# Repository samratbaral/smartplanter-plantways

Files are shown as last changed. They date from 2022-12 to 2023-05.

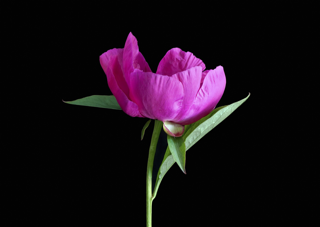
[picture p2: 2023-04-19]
src/plantways_app/Plantways-Application_client_20230317025249/assets/backgrounds/plant-purple.png

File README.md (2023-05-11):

# Smart Planter: PlantWays

Its an IOT(Internet of Things) project using Flutter development environment.
Please see the [Blog Post](https://blog.uta.edu/cseseniordesign/2023/05/10/smart-planter/) of Smart-Planter.
#
## Getting Started

Please see the [Getting Started](/src/plantsways_app/README.md) section for instructions on how to get started with this project.
#
## Summary
Please see the [Summary](/doc/summary/summary.md) of project.
#
## Design
Please see the [Design](/doc/design/3D%20print/) of project.
#
## Documentation
Please see the [Documents](/doc/documents/overleaf.md) of project.
#
## Source Code
Please see source code of the
- **[Smart Planter IoT](/src/plantsways_iot/)** and
- **[Flutter Phone Application for iOS and Android](/src/Plantways-Application_client_20230317025249/)**

For more information click [Read About the Project.](/src/README.md)
#

## Team

Our Team followed this [Contribute Guide](/CONTRIBUTE) for development information. If you have any questions, please contact by clicking the email.

**Samrat Baral:**[`samrat.baral[at] mavs [dot] uta [dot] edu`](mailto:samrat.baral@mavs.uta.edu)

**Samuel J Ruiz :**[`samuel.ruiz3[at] mavs [dot] uta [dot] edu`](mailto:samuel.ruiz3@mavs.uta.edu)

**Luis Guillermo Jaen:**[`luis.jaen[at] mavs [dot] uta [dot] edu`](mailto:luis.jaen@mavs.uta.edu)

**Don Dui:** [`don.bui[at] mavs [dot] uta [dot] edu`](mailto:don.bui@mavs.uta.edu)

**Kevin Eduardo Flores:**[`kevin.flores[at] mavs [dot] uta [dot] edu`](mailto:kevin.flores@mavs.uta.edu)

#
**NOTE: I have written this README using declarative sentences as it might appear when published. However some parts are not implemented yet.**
#

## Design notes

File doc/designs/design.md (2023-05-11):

### [< Back](/README.md) to README File.
# Design and Modeling

#### **Requirement: [LICENSE](/LICENSE), [CITATION](/CITATION.CFF)**, [AUTHORIZATION & PERMISSION](https://www.overleaf.com/login)

## **[Pot Design v1.0](/doc/design/3D%20print/Version%201/)**
This our recent Version 1.0 of 3D Design which was used to developed and tested our Smart Planter Pot. Follow the directions to view the 3D CAT Design File. or check the **[STL](/doc/design/3D%20print/Version%201/)** format.

## **[Pot Design v2.0](/doc/design/3D%20print/Version%202/)**
This our recent Version 2.0 of 3D Design which was used to developed and tested our Smart Planter Pot. Follow the directions to view the 3D CAT Design File. or check the **[STL](/doc/design/3D%20print/Version%202/)** format.

## **[Pot Design v3.0](/doc/design/3D%20print/Version%203/)**
This our recent Version 3.0 of 3D Design which was used to developed and tested our Smart Planter Pot. Follow the directions to view the 3D CAT Design File. or check the **[STL](/doc/design/3D%20print/Version%203/)** format.

#

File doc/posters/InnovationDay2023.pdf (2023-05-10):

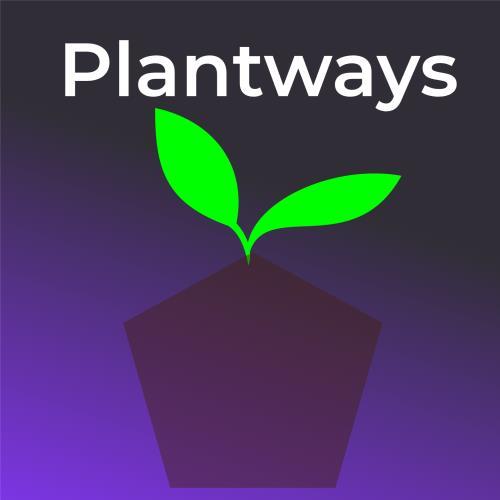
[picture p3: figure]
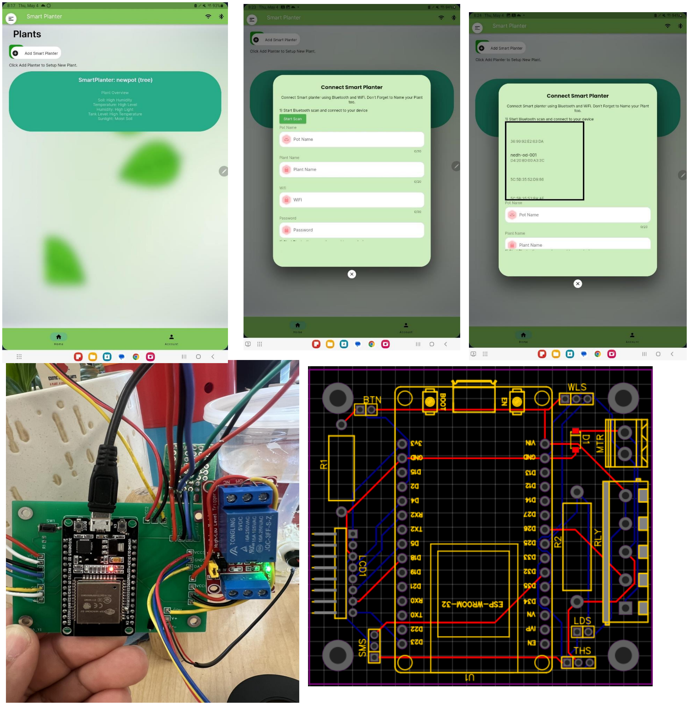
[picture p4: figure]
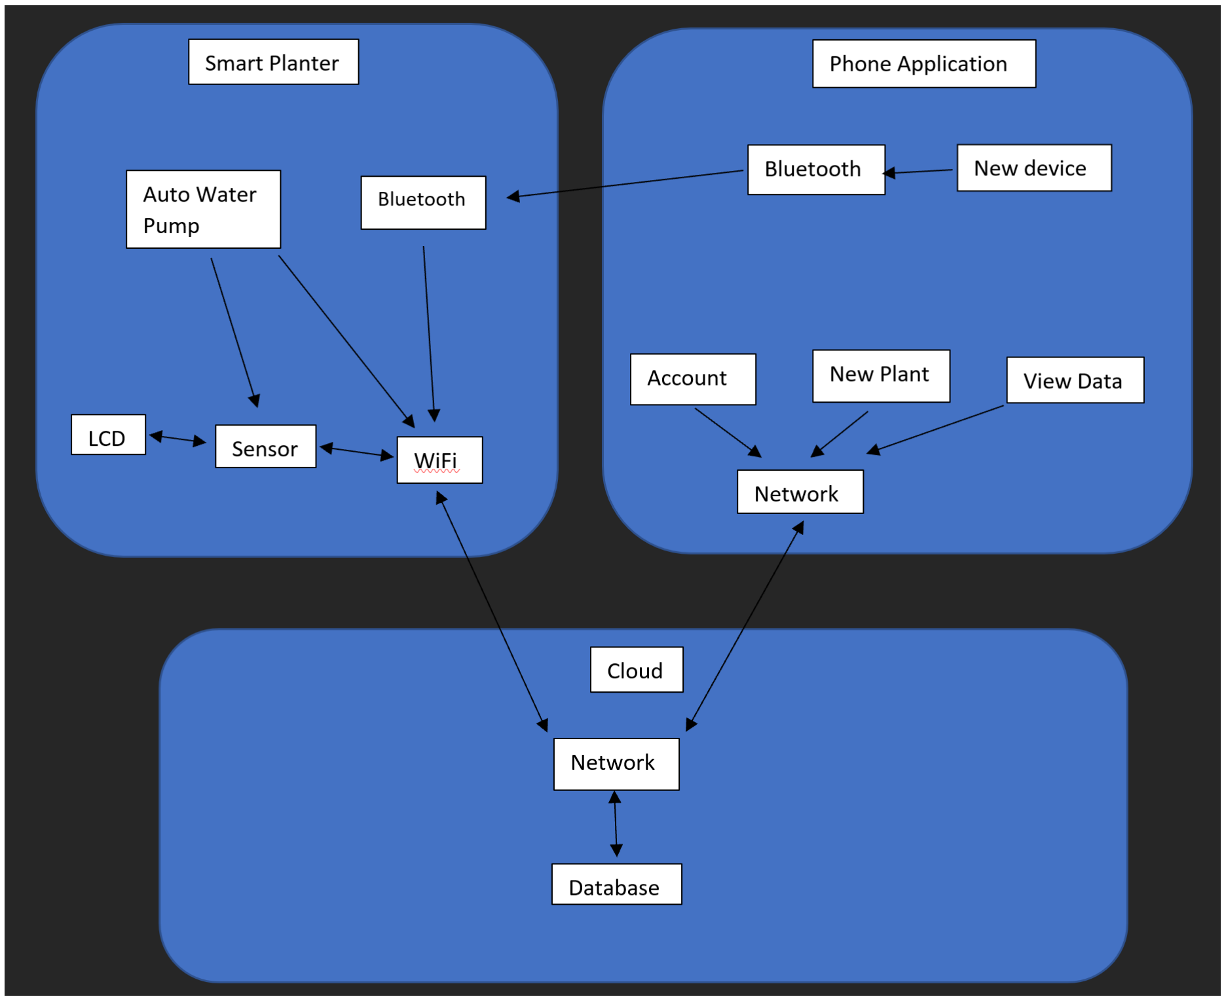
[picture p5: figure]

2023 UTA College of Engineering Innovation Day | April 18, 2023

Ruiz, S., Flores, K., Baral, S., Bui, D., Jaen, L.

# Smart Planter

Executive Summary | Key Requirements

### Background

We are going to build a self-watering plant pot, removing the consistent maintenance required in watering a house plant on your own. This pot is called the Smart Planter. The Smart Planter will measure humidity, temperature, and light exposure. We will also build an application to interface with the planter, to monitor the state for the individual plant(s). The hardware will consist of a printed circuit board and ESP32 microcontroller to minimize the size and cost of the pot.

The smart planter will solve many of the problems when it comes to doing maintenance on plants. People who have plants sitting in their house tend to forget or have a busy work schedule to take care of the plant. Therefore, the plant ends up dying, so the smart planter could be used by people who like having plants around them but do not like to take care of the plant often. The smart planter application can also be used as a learning tool for people who do not know anything about taking care of plants and want to learn how to take care of their plant by utilizing a cloud database which obtains information about the plant. For instance, some might not know how often to water a plant, so they sometimes over-water or under-water a plant, causing harmful deficiencies, which can lead to the death of the plant. Additionally, new plant caretakers could unknowingly keep their plant in an environment that’s too warm or cold for that specific species, or too dark/bright for the plant, which can also be harmful. The smart planter’s automation would remove these issues and ensure the longevity of the user's plant. The smart planter cloud database will have information about different plants, the user can pick the type of plant they are planting in the smart planter. The smart planter is designed to be used in a regular household but can also be retooled to use in a small commercial setting to grow plants on a small scale in a green house. The purpose of the smart planter is to be affordable and decorative to the public. There are some IoT planters out there, but they are expensive or have a self-watering system outside of the pot. The smart planter is supposed to combine the self-watering and IoT pot in one for ease of use.

User Interface: The Smart Planter will include a phone application that the user can use to monitor their plant. The phone application must include a user account creation section before the user is allowed to connect to their device(s). Wi-Fi/Bluetooth: The Smart Planter app must allow the users to pair to their Smart Planter device and link the device to their local network by providing their Wi-Fi name and password. Once the device is paired and set up, all the paired devices will be displayed on the home screen.
Plant Pot: The plant pot will be a 3D print design incorporating all the circuitry inside and include a refillable water tank. The design must include designated section to install the plant sensors, power cable and a reset button.
Auto Watering: The Smart Planter must be self-watering. The water pump must activate when the soil moisture indicates the plant needs water and will stop once the sensor indicates the ideal soil moisture is met.
LCD screen: The design of the plant pot will have an LCD screen in the front that must include the local time, low water tank notification, and a slideshow of sensor data.
Sensors:
- Light sensor
- Temperature sensor
- Humidity sensor
- Water level sensor

### Architectural Design Specifications

### Experimental Results

### References

### Conclusions

In the phone application subsystem, the user would be able to connect to the smart planter subsystem via Bluetooth whenever they press the new device button in their application. Once connected, they can set up their planter with their home Wi-Fi. Once their account and planter are set up both devices are connected to the network where they can send and receive data from the database. The Smart Planter sends sensor data to the LCD screen to display and to the database via Wi-Fi. The Water Pump component detects water level in the tank and sends it to sensor data. In the phone application subsystem users can view plant data, account information and plant list.

Current state of project: We currently have completed three 3D design prototypes, the initial design, the redesign, and the second larger version of the redesign. We also are done with the circuitry, and are missing some UI components, like the plant list and notification page. Currently the home page shows static values of a user's plants.

Future implementation: The finalization of the rest of the UI, like improving the user experience and stylization of the app. Completing all
the database components and making sure the correct data is sent to and from the database. Finally, completing the 3D pot most recent prototype, with complete app connectivity. We also plan on adding a list page of all the available plants to use on the pot, and a notification page which lets the user know when the water tank is low or if any of the sensor data doesn't meet the
recommended conditions for that specific plant.
- Dart Packages, https://pub.dev/.
- “The Developer Data Platform.” MongoDB, https://www.mongodb.com/.
- “Flutter Charts - Javatpoint.” Www.javatpoint.com, https://www.javatpoint.com/flutter-charts.
- Flutter Mapp, https://fluttermapp.com/.
- “Greatscott!” YouTube, YouTube, https://www.youtube.com/@greatscottlab.
- “DroneBot Workshop” YouTube, YouTube, (51) DroneBot Workshop - YouTube (https://www.youtube.com/@Dronebotworkshop)

## CSE Senior Design

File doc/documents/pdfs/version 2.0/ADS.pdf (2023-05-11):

## DEPARTMENT OF COMPUTER SCIENCE & ENGINEERING

## THE UNIVERSITY OF TEXAS AT ARLINGTON

## ARCHITECTURAL DESIGN SPECIFICATION

# CSE 4317: SENIOR DESIGN II SPRING 2023

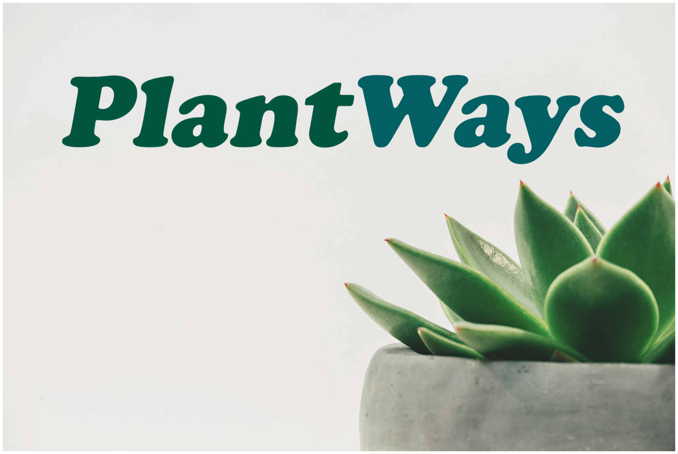
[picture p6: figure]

## PLANT WAYS

## SMARTPLANTER

SAMUEL J RUIZ
KEVIN FLORES
LUIS GUILLERMO JAEN
DON BUI
SAMRAT BARAL
Plant Ways - Spring 2023 | page 1 of 22

REVISION HISTORY

Revision | Date | Author(s) | Description
0.1 | 10.28.2022 | KF,DB,SR,LJ,SB | document creation
1.0 | 11.07.2022 | KF,DB,SR,LJ,SB | complete draft
2.0 | 12.14.2022 | KF,DB,SR,LJ,SB | final version

CONTENTS

1 Introduction | 5
2 System Overview | 6
3 Subsystem Definitions & Data Flow | 8
4 Smart Planter Subsystems | 9
5 User Interface Layer Subsystem | 15
6 Cloud Layer Subsystems | 21

LIST OF FIGURES

1 | SmartPlanter architectural layer diagram | | 6
2 | Sub-system overview | | 8
3 | Subsystem description diagram | | 9
4 | Subsystem description diagram | | 10
5 | Subsystem description diagram | | 11
6 | Subsystem description diagram | | 12
7 | Subsystem description diagram | | 13
8 | Setup subsystem description diagram | | 15
9 | Setup subsystem | | 16
10 | Account subsystem | | 18
11 | Network subsystem | | 19
12 | Cloud subsystem description diagram | | 21
13 | Cloud subsystem description diagram | | 22

LIST OF TABLES

2 | Water pump interfaces | | 10
3 | Sensors interfaces | | 11
4 | WiFi interfaces | | 12
5 | Bluetooth interfaces | | 13
6 | LCD Screen interfaces | | 14
7 | Setup Subsystem Interfaces | | 17
8 | Account Subsystem Interfaces | | 18
9 | Network Subsystem Interfaces | | 20
10 | Cloud Network Interfaces | | 21
11 | Cloud Database interfaces | | 22

### 1 INTRODUCTION

The SmartPlanter is a product intended to ease plant maintenance by monitoring the plants environment and automating the watering process. The SmartPlanter will require a mobile application that allows users to pair their SmartPlanter device to the internet. Using the mobile application, the users can set the sensor calibration data for the specific plant they are planting. The SmartPlanter device will be able to monitor the plant’s environment using the sensors and the calibration data in order to automate the watering process when the soil is too dry.

### 2 SYSTEM OVERVIEW

The SmartPlanter has three layers which consist of the SmartPlanter Layer, the User Interface layer or Phone Application Layer, and the Cloud Layer. The SmartPlanter layer consist of the physical plant pot and includes the micro-controller, water tank, sensors and LCD screen. The SmartPlanter layer monitors the plant’s environment and provides automatic watering. This layer also provides data to the Cloud Layer for storage. The User interface layer consist of a mobile phone application where the settings for the pot can be selected. This settings can be applied directly to the SmartPlanter Layer by communicating by Bluetooth. The User Interface layer can also access the SmartPlanter through the cloud layer using WiFi.

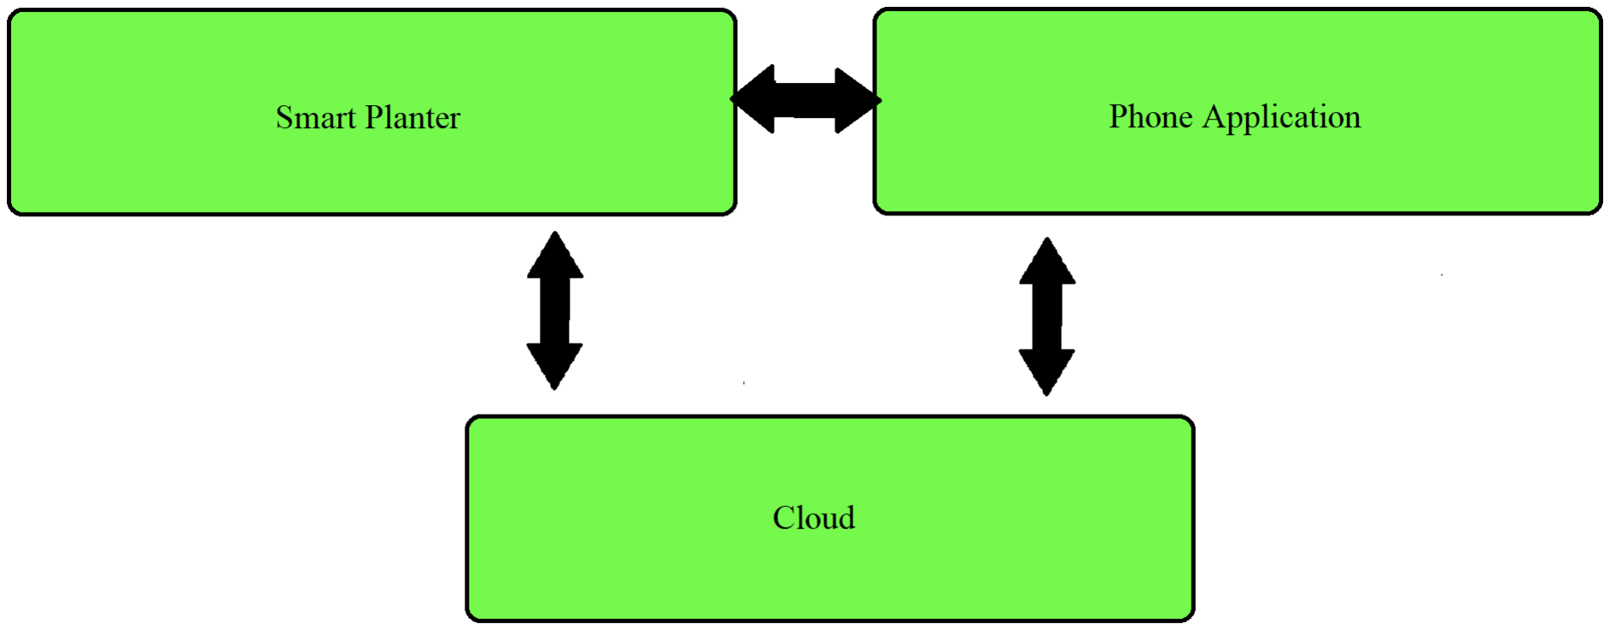
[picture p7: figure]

Figure 1: SmartPlanter architectural layer diagram

### 2.1 SMARTPLANTER

The SmartPlanter will have a display on the pot, that will let the user switch the display to show the current time. The SmartPlanter pot will have WiFi and Bluetooth. The WiFi is used to connect to the database and to upload data collected from the sensors. The Bluetooth feature will be used for the initial setup to connect it to the WiFi. The SmartPlanter pot will have a water pump used to water the plant when the soil moisture is detected low. The SmartPlanter will also include a light detector, a humidity and temperature sensor to monitor the average environment the plant is currently in and will upload the average data to the database. A water level detector will also be used to monitor the water tank level and assure it does not run below the minimum threshold. An LCD screen will also be included in the front of the SmartPlanter pot that displays either the name of the plant or the current time.

### 2.2 USER INTERFACE

The User Interface layer consist of mobile phone application that interfaces with the SmartPlanter via Bluetooth and the cloud via WiFi . The main usage of Bluetooth consist of the initial device set up to connect the SmartPlanter to the home network. The application will consist of an account subsystem to allow the user to change settings. The phone application can also change the calibration data of the SmartPlanter by adding custom settings catered to the plant they are growing. This is performed by allowing the user to connect to the cloud layer and view a database of plants. When this information is selected, it will store those calibration settings in the database and into the local storage of the Smart-

Planter. The application can also view the current environmental conditions of the plant by connecting to the cloud through the network and then accessing the SmartPlanter.

### 2.3 CLOUD

The Cloud Layer consist of a database used to store plant sensor data from the SmartPlanter and user account settings from the User Interface Layer. The database will also store hard-coded plant information that the user will be able to retrieve via the mobile phone application.

### 3 SUBSYSTEM DEFINITIONS & DATA FLOW

The user would be able to connect to the smart planter through Bluetooth whenever they press the new device button in their application once connected they can set up their planter with their home WiFi. Once their account and planter are set up both devices are connected to the network where they can send and receive data from the database.

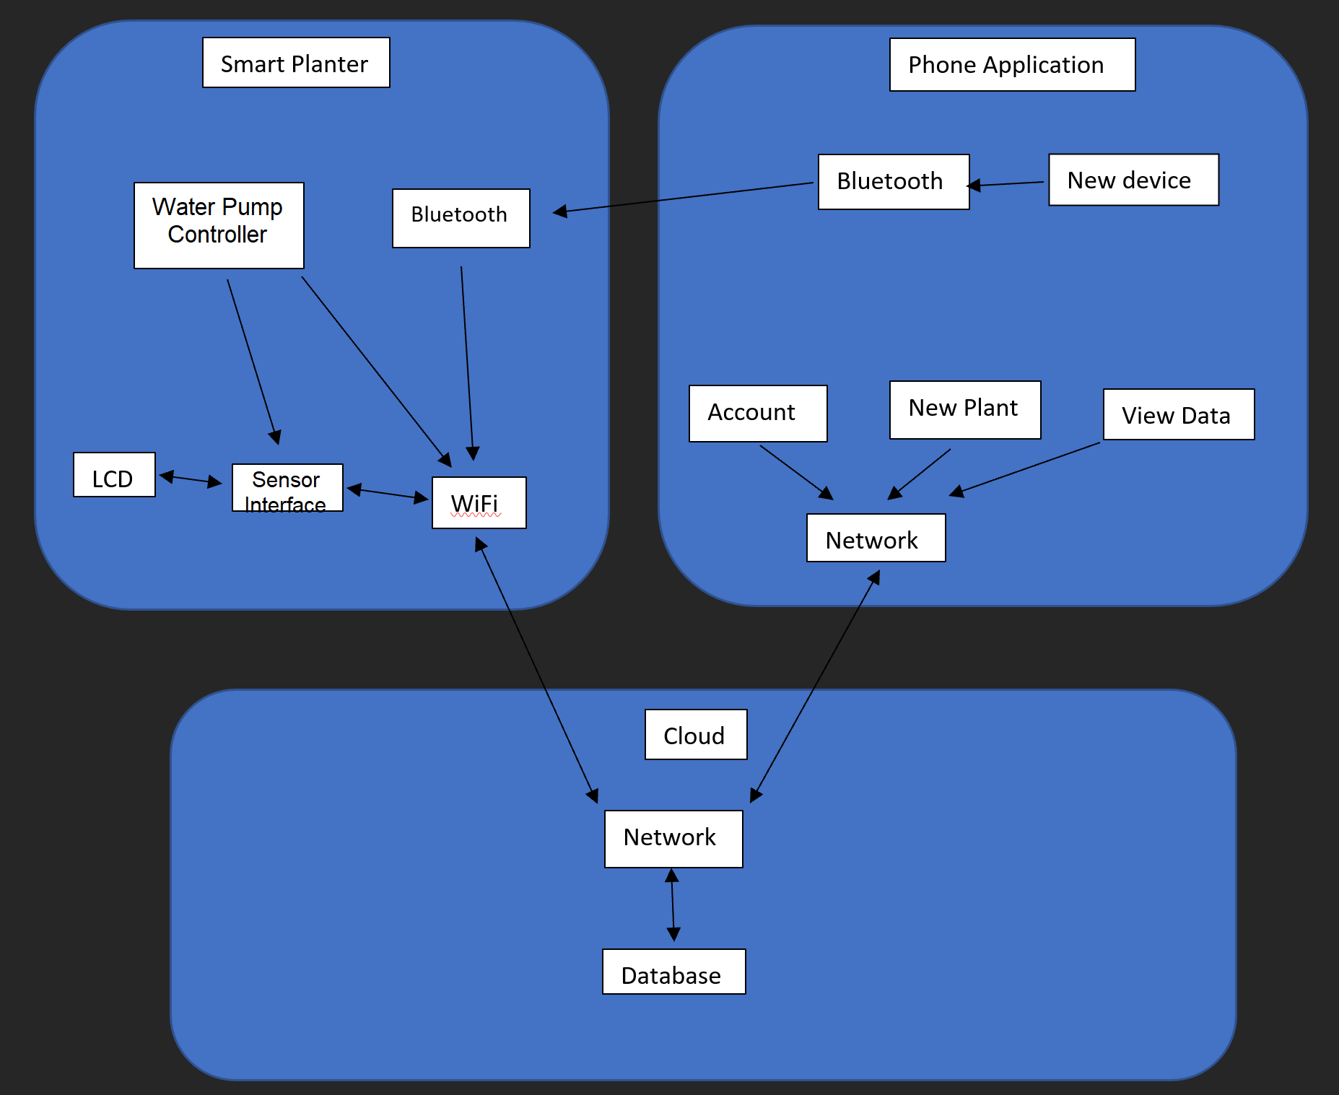
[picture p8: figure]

Figure 2: Sub-system overview

### 4 SMART PLANTER SUBSYSTEMS

The Smart Planter layer is made up of 5 different subsystems which gather information, communicate with other important functions like watering and online data, and display information to the user. The subsystems are the following: auto water pump system, sensor system, Bluetooth, WiFi, and the LCD screen.

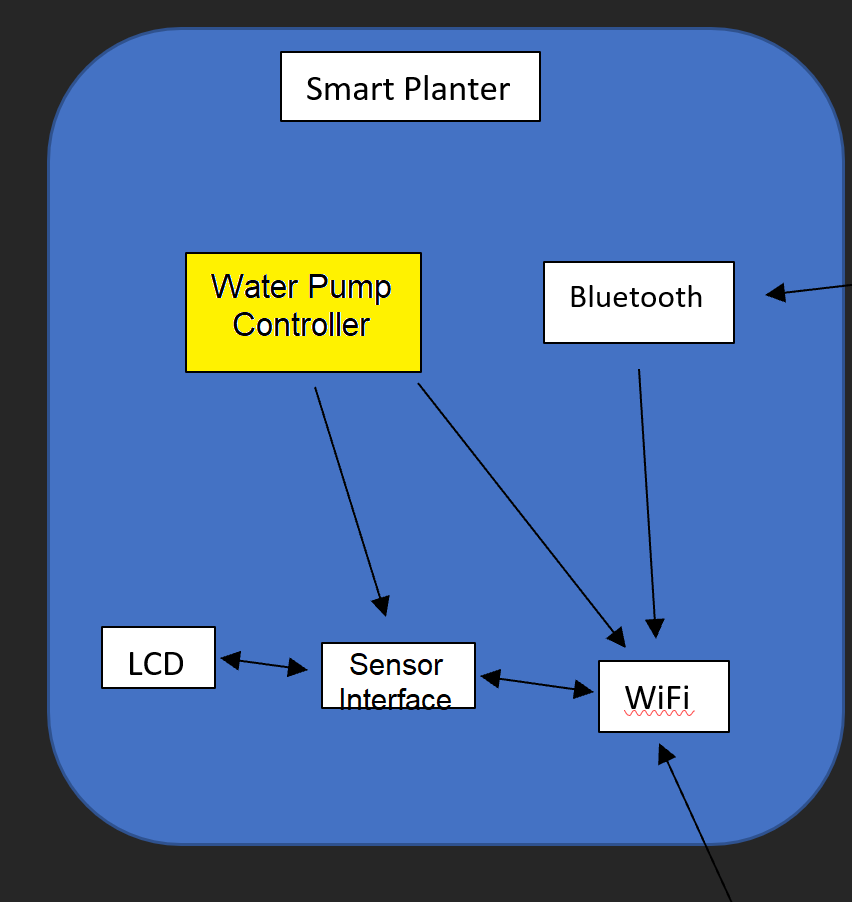
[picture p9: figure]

Figure 3: Subsystem description diagram

### 4.1 AUTO WATER PUMP

The auto water pump subsystem is in charge of watering the plant and keeping the plant at a sufficient level of moisture. It communicates with the sensors in the planter, receiving the instruction to pump water.

### 4.1.1 ASSUMPTIONS

We assume the water pump successfully receives the signal to water the planter from the moisture sensor.

### 4.1.2 RESPONSIBILITIES

This water pump subsystem is responsible for keeping the plant at a sufficient level of moisture. When the soil runs too dry, the water pump will receive a signal from the moisture sensor, which will initiate the process of pumping the water into the soil.

### 4.1.3 WATER PUMP INTERFACES

Table 2: Water pump interfaces

ID | Description | Inputs | Outputs
#01 | Moisture Sensor | moisture level | water instruction

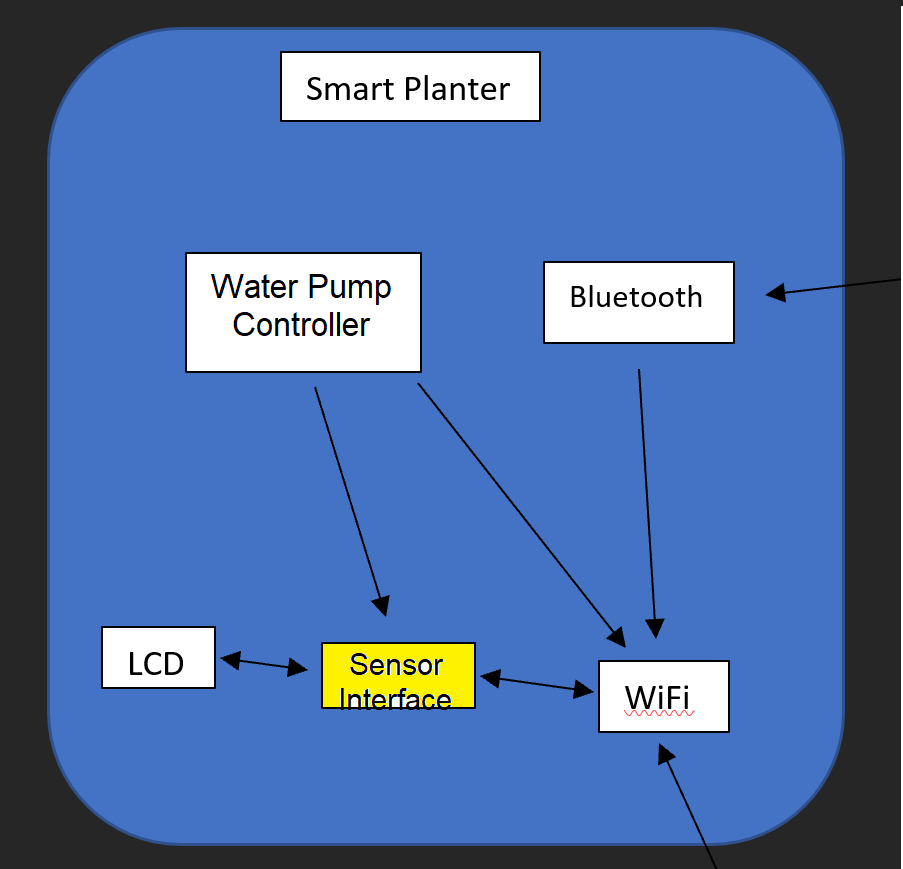
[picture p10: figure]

Figure 4: Subsystem description diagram

### 4.2 SENSORS

The sensors in our smart planter collect external and internal data which is used to monitor the current status of the plant. The sensors include: light, humidity, temperature, and soil moisture. The soil moisture sensor communicates with the water pump, telling it when to pump water, and the other 3 sensors send their data through WiFi to our cloud.

### 4.2.1 ASSUMPTIONS

We assume all of the sensors operate accurately, and correctly record data on the external and internal environments.

### 4.2.2 RESPONSIBILITIES

The light sensors are responsible for gathering data from the smart planter’s light environment, recording the light exposure on the plant. The humidity and temperature sensors are responsible for recording the humidity and temperature of the environment. The soil moisture sensor is in charge of keeping track of the moisture levels of the soil, notifying the water pump to water when the soil is too dry. All of these sensors communicate with our cloud database through WiFi.

### 4.2.3 SENSORS INTERFACES

Table 3: Sensors interfaces

ID | Description | Inputs | Outputs
#01 | Water Pump | power on for pump | water the planter

#01 | WiFi | Humidity, Temper-ature, Light Expo-sure Data | send data to cloud

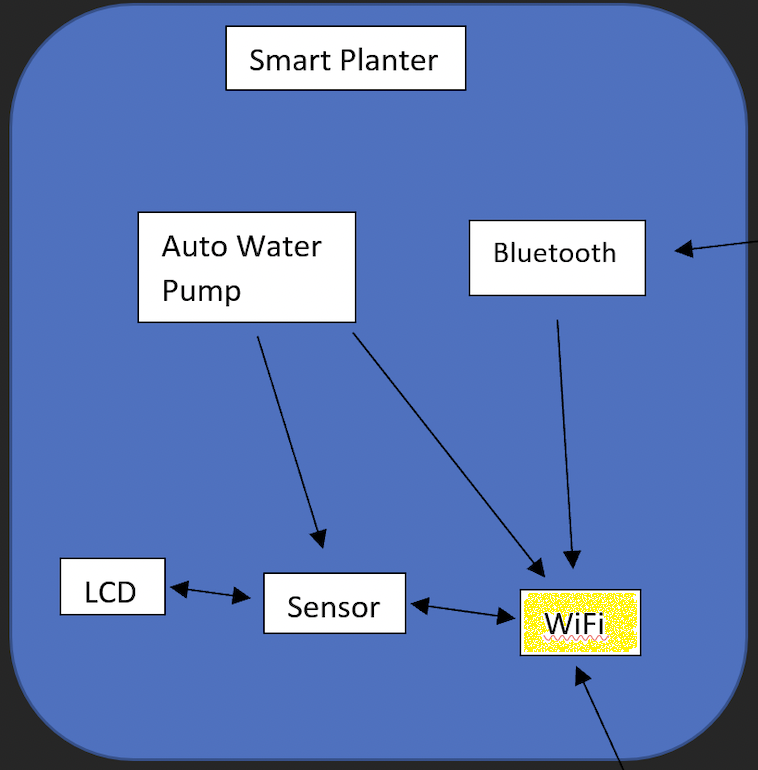
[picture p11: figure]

Figure 5: Subsystem description diagram

### 4.3 WIFI

The WiFi component of our smart planter deals with receiving all of the data from the external and internal sensors, and then sending that data off to the cloud database. The WiFi communicates with the sensor subsystem and the LCD screen.

### 4.3.1 ASSUMPTIONS

We assume the networks are up and fully operational, and that there are no obstructions to the transmission of data.

### 4.3.2 RESPONSIBILITIES

The WiFi system is responsible for receiving the light exposure, temperature, and humidity levels, and sending them over to the cloud database. It is also responsible for receiving the current time from the network and sending it over to the LCD screen.

### 4.3.3 WIFI INTERFACES

Table 4: WiFi interfaces

ID | Description | Inputs | Outputs
#01 | Light Sensor | exposed light | lumen value

#02 | Humidity Sensor | environment hu-midity | humidity percent-age

#03 | Temperature Sensor | environment tem-perature | degrees Fahren-heit

#04 | LCD Screen | current time or plant name | current time or plant name on the screen

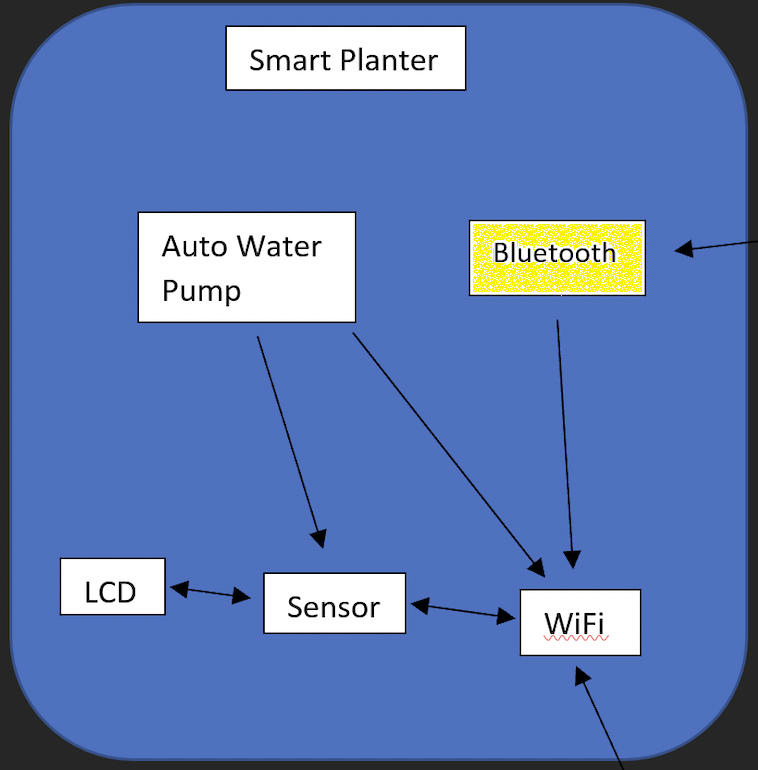
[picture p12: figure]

Figure 6: Subsystem description diagram

### 4.4 BLUETOOTH

The Bluetooth system is there to establish a connection between the smart planter and the network, via your smart phone. The Bluetooth communicates with the WiFi subsystem.

### 4.4.1 ASSUMPTIONS

We assume the Bluetooth technology is properly establishing connections between the smart planter and network.

### 4.4.2 RESPONSIBILITIES

The Bluetooth is responsible for establishing the network connection between the smart planter and WiFi, by using your smart phone to input the required information.

### 4.4.3 BLUETOOTH INTERFACES

Table 5: Bluetooth interfaces

ID | Description | Inputs | Outputs
#01 | Smart Phone | Bluetooth creden-tials | WiFi credentials

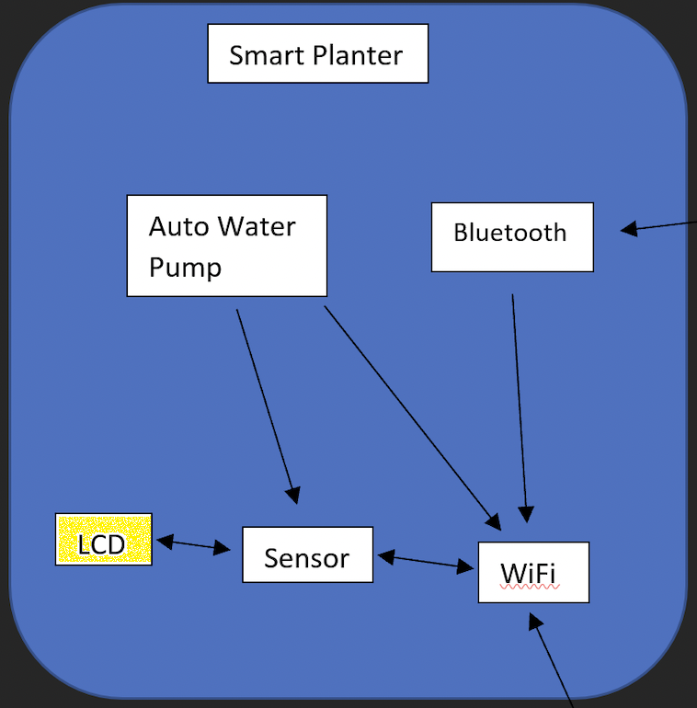
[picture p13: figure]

Figure 7: Subsystem description diagram

### 4.5 LCD SCREEN

The LCD screen is used to display either the current time or the name of your plant. The LCD screen communicates with the WiFi subsystem, receiving necessary data.

### 4.5.1 ASSUMPTIONS

We assume the LCD screen is posting the accurate plant name choice from the user, or the current time.

### 4.5.2 RESPONSIBILITIES

The LCD screen is responsible for displaying the current accurate time or name of the plant. It’s responsible for communicating with the WiFi, in order to receive the data it needs to display.

### 4.5.3 LCD SCREEN INTERFACES

Table 6: LCD Screen interfaces

ID | Description | Inputs | Outputs
#01 | WiFi | name created by the user or time chosen | Plant Name or Current Time

### 5 USER INTERFACE LAYER SUBSYSTEM

In this section, the user interface is layout where user can observe and optimize the smart planter pot. This is an application layer from the main system where users are required to create an account, where user must acknowledge and accept term and conditions to use the application in their mobile devices and its features. The application will be a GUI mobile app or mobile website GUI application the user can visit to have a unique experience.

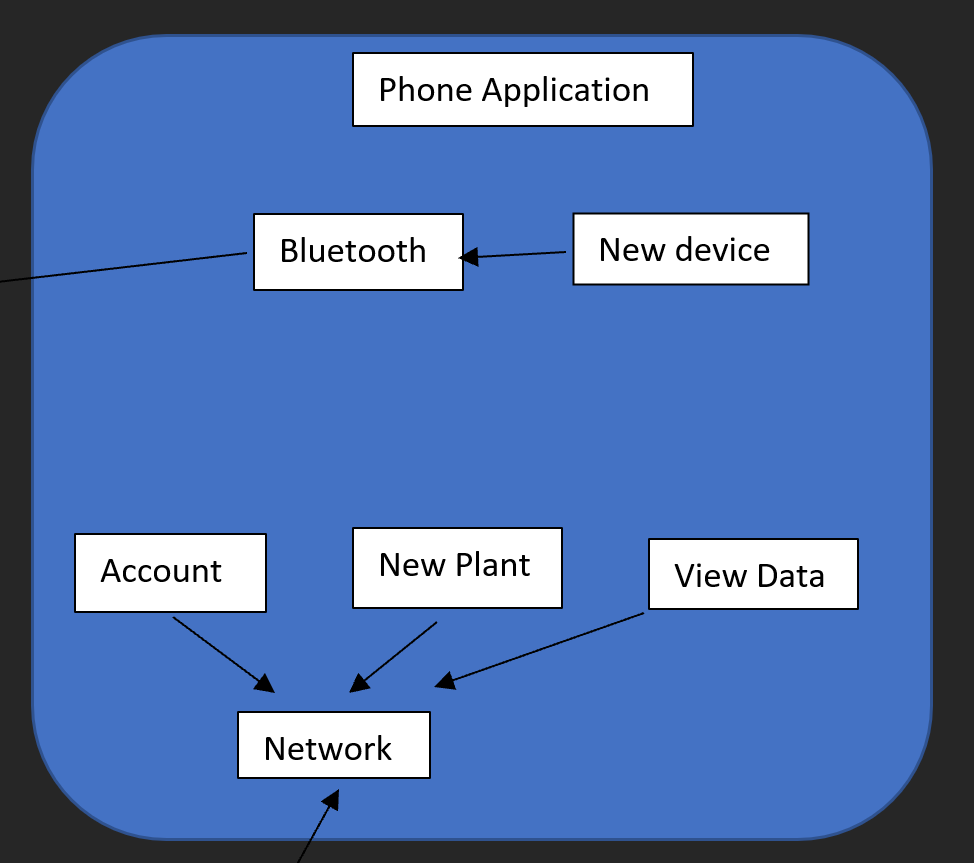
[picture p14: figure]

Figure 8: Setup subsystem description diagram

### 5.1 SETUP LAYER SUBSYSTEM

This subsystem is a setup process for a user to use smart planter pot. The user is required to agree the smart planter terms and condition so that user can register and setup their account with smart planter. The user is given registration form where user is required to input some information while other information could be optional which gives user personalized system setting while using the application.

### 5.1.1 ASSUMPTIONS

The user is assumed to have a device which is WiFi and Bluetooth enable which should be running recent Android (Version 13.0) or iOS (Version 16.0) operating system can should be capable to connect to the internet. We also assume that user read all terms and conditions before registering and using the smart planter service.

### 5.1.2 RESPONSIBILITIES

This sub-layer is responsible creating a account for a user so they can use the smart planter pot. The account creation is important for the process to have control over. After the account is created it will interact with the pot "Smart Planter Layer" and database from the "Cloud Layer" for privacy, usage and safety of the user and the application.

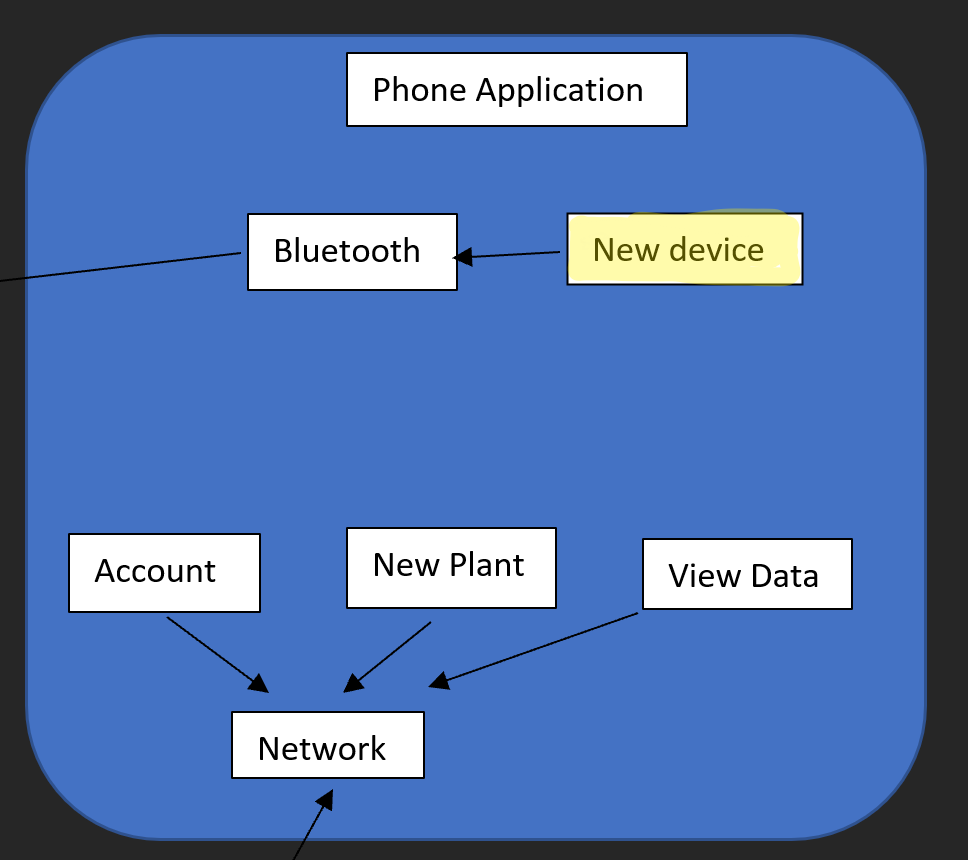
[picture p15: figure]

Figure 9: Setup subsystem

### 5.1.3 SUBSYSTEM INTERFACES

Since, This sub-layer is responsible creating a account for a user. The following are important inputs and outputs for the subsystem in the table entry for each labeled interface that connects to this subsystem. For each entry, describe any incoming and outgoing data elements will pass through this interface.

Table 7: Setup Subsystem Interfaces

ID | Description | Inputs | Outputs
#01 | User Setup (Register Form) | User Id Username First Name Last Name Email Phone Number Password Confirm Password | User Data Created

#02 | Device Setup (Register Form) | Device Id Device Name Device Picture Device Information Device Data | Device Data Created

#03 | Cloud Setup (Automatic) | User Setup Data Device Setup Data | Cloud Data Created

### 5.2 ACCOUNT SUBSYSTEM LAYER

This subsystem is a user account after setup for a registered user to use smart planter pot. The user is required to log-in so that user can use their account with their own smart planter. The user is given login form where user is required to input user credential which gives user personalized system setting while using the application.

### 5.2.1 ASSUMPTIONS

The user is assumed to have the Smart Planter mobile application is downloaded from recent Android (Version 13.0) or iOS (Version 16.0) operating system which should be capable to connect to the internet from the device using WiFi and Bluetooth enable.

### 5.2.2 RESPONSIBILITIES

This sub-layer is responsible for logging a user so they can use smart planter pot. After the user is logged in it will interact with the pot "Smart Planter Layer" and database from the "Cloud Layer" for privacy, usage and safety of the user and the application.

### 5.2.3 SUBSYSTEM INTERFACES

Since, This sub-layer is responsible logging a current account of a user. The following are important inputs and outputs for the subsystem in the table entry for each labelled interface that connects to this subsystem. For each entry, describe any incoming and outgoing data elements will pass through this interface.

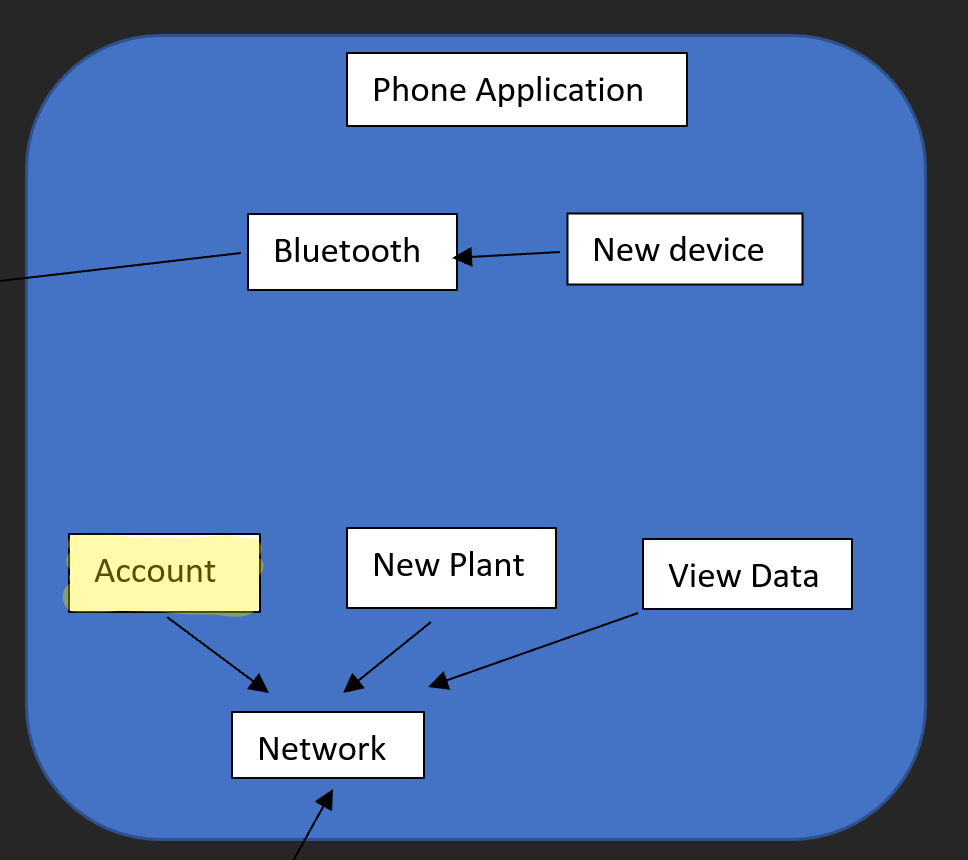
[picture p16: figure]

Figure 10: Account subsystem

Table 8: Account Subsystem Interfaces

ID | Description | Inputs | Outputs
#01 | User Validation (Login Form) | Username or Email Password | User Authentication

#03 | Pot Data (Automatic) | N/A | User Device Data

### 5.3 NETWORK SUBSYSTEM LAYER

This subsystem is a connection process for a user to use smart planter pot. The user will automatically fetch data from the database as well as it can calibrate and configure the device using internet via WiFi. The user is given registration form where user is required to input some information while other information could be optional which gives user personalized system setting while using the application.

### 5.3.1 ASSUMPTIONS

The user are assumed to have a device which is WiFi and Bluetooth enable which should be running recent Android (Version 13.0) or iOS (Version 16.0) operating system with the Smart Planter mobile application which is logged-in user which is capable of connecting to the internet.

### 5.3.2 RESPONSIBILITIES

This sub-layer is responsible connecting a account for a user so they can use the smart planter pot online. After the account is connected it will interact with the pot "Smart Planter Layer" and database from the "Cloud Layer" for any data exchange.

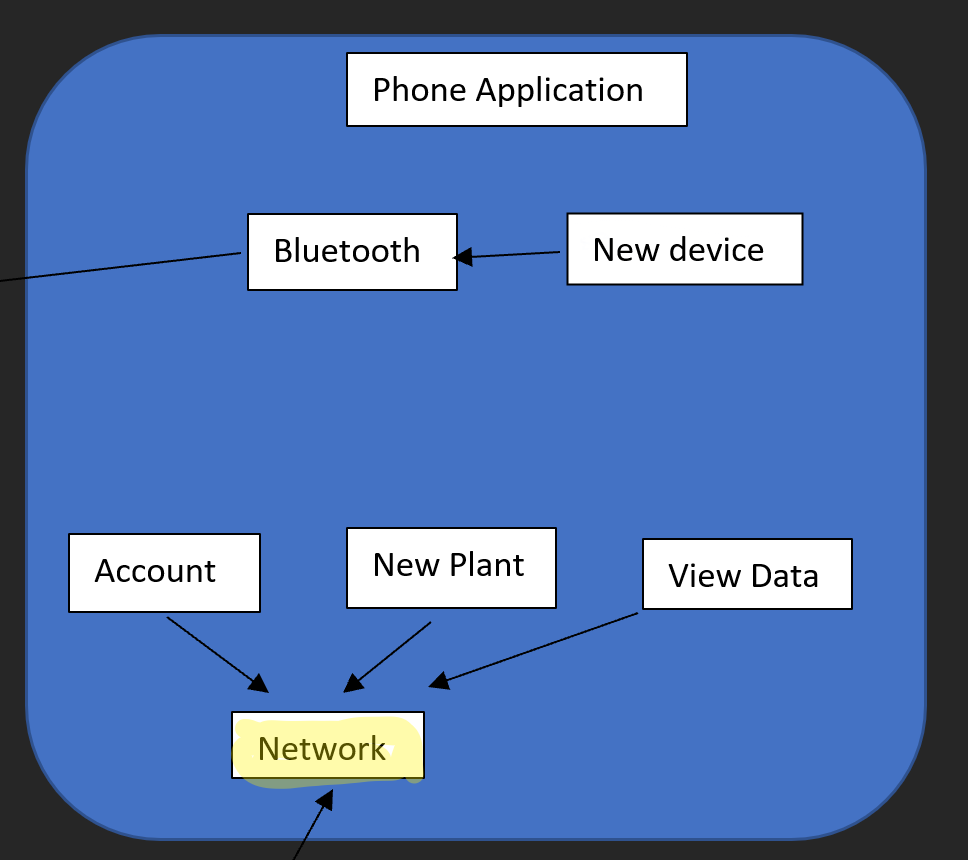
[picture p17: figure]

Figure 11: Network subsystem

### 5.3.3 SUBSYSTEM INTERFACES

Since, This sub-layer is responsible for connecting a account of a user. The follow are important inputs and outputs for the subsystem in the table entry for each labelled interface that connects to this subsystem. For each entry, describe any incoming and outgoing data elements will pass through this interface.

Table 9: Network Subsystem Interfaces

ID | Description | Inputs | Outputs
#01 | User Data (Register Form) | User Id Username First Name Last Name Email Phone Number Password | User Data Added

#02 | Device Data (Register Form) | Device Id Device Name Device Picture Device Information Device Data | Device Data Added

#03 | Cloud Data (Added Automatically) | User Setup Data Device Setup Data | Cloud Data Added

#04 | Authentication (Login Form) | Username or Email Password | User Validated

#05 | Pot Data (Automatic) | Device Data Request | Device Data Received

### 6 CLOUD LAYER SUBSYSTEMS

The smart planter layers is made up with network and the database, the could will communicating between the database throw the network connecting to the smart planter pot system. The smart planter pot will send data from the sensor throw the network connected to the database to be store.

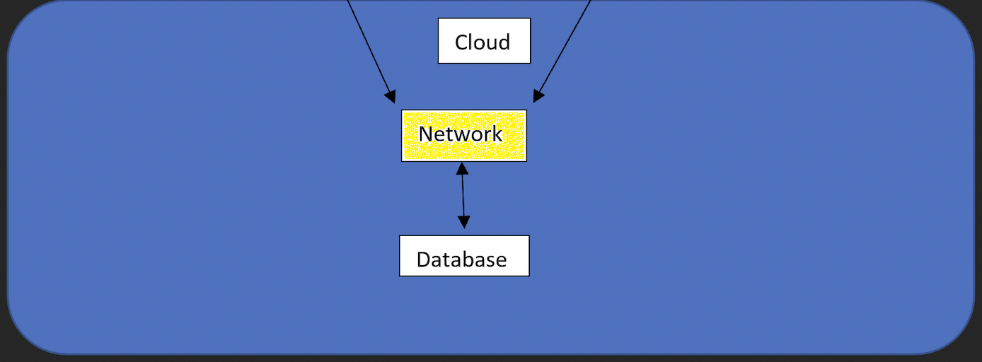
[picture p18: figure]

Figure 12: Cloud subsystem description diagram

### 6.1 NETWORK

The network is in charge of the communication between the non-sequel database(MongoDB Database), smart planter application(Mobile Application) and the smart planter system(Smart Planter Pot).

### 6.1.1 ASSUMPTIONS

In the cloud layer we have plug-in connection to the database network into the flutter application and the smart planter pot which will have reliable network connection via WiFi and potentially using Bluetooth. Using the network connection of cloud we send, receive and store the passing data around the network.

### 6.1.2 RESPONSIBILITIES

The network in responsible the communication between between the non-sequel database(MongoDB Database), smart planter application(Mobile Application) and the smart planter system(Smart Planter Pot), the network in charge making sure the data get to the database without any lost of data packet and retrieve from the data from the database when needed.

### 6.1.3 SUBSYSTEM INTERFACES

In the cloud network interfaces we have two type of input and output connection that gets input from two different networks. First, the critical input connection from plot data which is clearly from the Layer Smart Planter which feeds data into specific data fields. Second, the connection to the network layer is from Layer Phone Application where the database specific fields are accessible format so that it could get fetched.

Table 10: Cloud Network Interfaces

ID | Description | Inputs | Outputs
#1 #2 | SmartPlanter Pot connected to Cloud Network Mobile Application Network connected to Cloud Network | Smart planter system data Database data replaced Fetch Database data | Store new data into database wait for Fetching data send new data

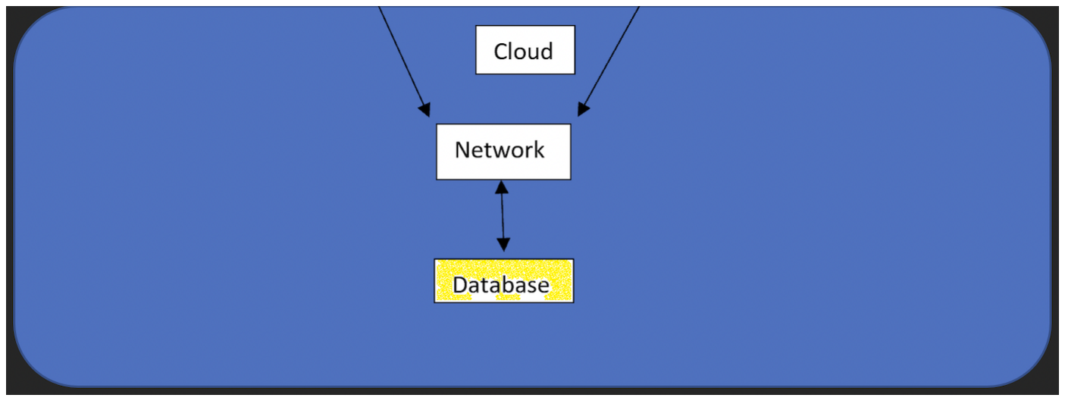
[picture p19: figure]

Figure 13: Cloud subsystem description diagram

### 6.2 DATABASE

The cloud database we are using is server-less which basically need no version control and everything is setup in cloud database is in charge holding data from the smart planter sensor that was send from the smart planter system and the database is also in charge of sending out requested data from the user.

### 6.2.1 ASSUMPTIONS

The database is responsible for storing data send from the smart planter system and the database is responsible sanding out data to the user when the data is request by them.

### 6.2.2 RESPONSIBILITIES

The database is responsibly is hold the data for the light sensor and the humidity sensor data and the temperature sensor data and the moisture sensor data and information about plant that user could look up. The database should be able to send data when it is request from the user.

### 6.2.3 SUBSYSTEM INTERFACES

In the database network interfaces we have two type of input and output connection that gets input from two different networks. First, the critical input connection from network plot data which update data into specific data fields. Second, the connection to the network layer is from Layer Phone Application where the database specific fields are accessible format so that it could get fetched.

Table 11: Cloud Database interfaces

ID | Description | Inputs | Outputs
#1 | Add New data | Update the database with new data fields | Sucess Message

#2 | Fetch data | Fetch the database with new data fields | Sucess Message

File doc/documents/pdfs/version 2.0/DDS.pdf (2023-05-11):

## DEPARTMENT OF COMPUTER SCIENCE & ENGINEERING

## THE UNIVERSITY OF TEXAS AT ARLINGTON

## DETAILED DESIGN SPECIFICATION

# CSE 4317: SENIOR DESIGN II SPRING 2023


## PLANTWAYS

## SMARTPLANTER

SAMUEL J RUIZ
KEVIN FLORES
LUIS GUILLERMO JAEN
DON BUI
SAMRAT BARAL
PlantWays - Spring 2023 | page 1 of 19

REVISION HISTORY

Revision | Date | Author(s) | Description
0.1 | 2.01.2023 | KF,DB,SR,LJ,SB | document creation
0.2 | 2.13.2023 | KF,DB,SR,LJ,SB | complete draft
1.0 | 5.10.2023 | KF,DB,SR,LJ,SB | Final Version

CONTENTS

1 Introduction | 5
2 System Overview | 5
3 SmartPlanter Subsystems | 6
4 User Interface Subsystems | 11
5 Cloud Subsystems | 16
6 Appendix A | 18

LIST OF FIGURES

1 | System architecture | | 5
2 | Automatic Water Pump Subsystem Diagram | | 6
3 | Sensor Subsystem Diagram | | 7
4 | WiFi Subsystem diagram | | 8
5 | Bluetooth Subsystem Diagram | | 9
6 | LCD Screen Subsystem Diagram | | 10
7 | New Device Subsystem Diagram | | 11
8 | Bluetooth Subsystem Diagram | | 12
9 | View Data Subsystem Diagram | | 13
10 | New Plant Subsystem Diagram | | 14
11 | Account Subsystem Diagram | | 15
12 | Network Subsystem Diagram | | 16
13 | Network Subsystem Diagram | | 16
14 | Database Subsystem Diagram | | 17

LIST OF TABLES

### 1 INTRODUCTION

As described in the ADS, the SmartPlanter is a product intended to ease plant maintenance by monitoring the plants environment and automating the watering process. The SmartPlanter will require a mobile application that allows users to pair their SmartPlanter device to the internet. Using the mobile application, the users can set the sensor calibration data for the specific plant they are planting. The SmartPlanter device will be able to monitor the plant’s environment using the sensors and the calibration data in order to automate the watering process when the soil is too dry.
In the system requirements specification document, we described how the SmartPlanter’s targeted audience are plant beginners and people who neglect plant care. The purpose of this device is for it to be used as a learning tool and to automate plant care. The mobile app’s purpose is to provide an easy using monitoring system for your plant.

### 2 SYSTEM OVERVIEW

There are 3 separate layers to our data flow diagram: Smart Planter, Phone Application, and Cloud. The phone application layer deals with the initial user’s set up and inputs, and provides the user with an interface to monitor the SmartPlanter’s data. This layer is then connected to the Smart Planter layer via Bluetooth, and then the WiFi connection is established. Finally, the user can send or request data, to and from the database via the cloud layer.


Figure 1: System architecture

### 3 SMARTPLANTER SUBSYSTEMS

### 3.1 LAYER HARDWARE

The SmartPlanter system is run on an ESP-32 micro-controller. What we use to make the smart planter pot, we use a software that is call Shapr3D to make the 3D model of smart planter pot and we use the Ender 3 3D printer to print out the 3D model. The smart planter pot will have LCD screen in front of the smart planter pot. We use Penpot to make the to make the graphic for the LCD screen that show the information level of the sensor.

### 3.2 LAYER OPERATING SYSTEM

### 3.3 LAYER SOFTWARE DEPENDENCIES

The SmartPlanter code is compiled using Arduino IDE and the EspressIf Arduino packages.

### 3.4 WATER PUMP CONTROLLER

The auto water pump subsystem is in charge of watering the plant and keeping the plant at a sufficient level of moisture. It communicates with the sensors in the planter, receiving the instruction to pump water.


Figure 2: Automatic Water Pump Subsystem Diagram

### 3.4.1 SUBSYSTEM HARDWARE

The water pump in the SmartPlanter is an: ALAMSCN 3v - 5v micro submersible mini water pump.

### 3.4.2 SUBSYSTEM OPERATING SYSTEM

### 3.4.3 SUBSYSTEM SOFTWARE DEPENDENCIES

### 3.4.4 SUBSYSTEM PROGRAMMING LANGUAGES

The code for the Automatic water pump was written in C using Arduino IDE.

### 3.4.5 SUBSYSTEM DATA STRUCTURES

### 3.4.6 SUBSYSTEM DATA PROCESSING

### 3.5 SENSOR INTERFACE

The sensors in the Smart Planter are used to monitor the plant’s environment by measuring the temperature, humidity, and soil moisture. When the soil moisture is low, the sensor data will notify the water pump and being the automatic watering. The water level sensor is used to assure the water pump does not run without any water.


Figure 3: Sensor Subsystem Diagram

### 3.5.1 SUBSYSTEM HARDWARE

The sensors in the SmartPlanter comprise of the soil moisture is monitored using a Songhe Capacitive Soul Moisture Sensor, the water tank level is monitored using an EPTTECH Food Grade Optical Infrared Water Liquid Level Sensor, and the Temperature + Humidity is monitored using a HiLetgo DHT11 Temperature Humidity Sensor Module.

### 3.5.2 SUBSYSTEM OPERATING SYSTEM

### 3.5.3 SUBSYSTEM SOFTWARE DEPENDENCIES

The SmartPlanter DHT11 uses the Arduino DHT Library.

### 3.5.4 SUBSYSTEM PROGRAMMING LANGUAGES

The code for the SmartPlanter Sensors is written in C.

### 3.5.5 SUBSYSTEM DATA STRUCTURES

Sensor Interface will read in DAC units

### 3.5.6 SUBSYSTEM DATA PROCESSING

Data being processes to LCD screen and database will be converted into strings corresponding the sensor status. (Water level sensor DAC of 0 will process "Water Full to database and LCD screen")

### 3.6 WIFI

The WiFi component of our smart planter deals with receiving all of the data from the external and internal sensors, and then sending that data off to the cloud database.


Figure 4: WiFi Subsystem diagram

### 3.6.1 SUBSYSTEM HARDWARE

The SmartPlanter is able to connect to the Wifi using the ESP-32 built in WiFi module.

### 3.6.2 SUBSYSTEM OPERATING SYSTEM

### 3.6.3 SUBSYSTEM SOFTWARE DEPENDENCIES

The set up for the WiFi uses the Arduino ESP-32 WiFi Manager library.

### 3.6.4 SUBSYSTEM PROGRAMMING LANGUAGES

The code for the SmartPlanter WiFi was written in C.

### 3.6.5 SUBSYSTEM DATA STRUCTURES

SmartPlanter sensor data will be automatically inserted into MangoDB which allows for the phone application to retrieve sensor data.

### 3.6.6 SUBSYSTEM DATA PROCESSING

Data send to the database from the ESP-32 will be in strings assigned in the sensor interface

### 3.7 BLUETOOTH

The Bluetooth system is there to establish a connection between the smart planter and the network, via your smart phone. The Bluetooth communicates with the WiFi subsystem.


Figure 5: Bluetooth Subsystem Diagram

### 3.7.1 SUBSYSTEM HARDWARE

The SmartPlanter is able to connect to the Wifi using the ESP-32 built in Bluetooth module.

### 3.7.2 SUBSYSTEM OPERATING SYSTEM

### 3.7.3 SUBSYSTEM SOFTWARE DEPENDENCIES

The set up for the Bluetooth uses the Arduino ESP-32 Bluetooth Serial library.

### 3.7.4 SUBSYSTEM PROGRAMMING LANGUAGES

The code for the SmartPlanter Bluetooth was written in C.

### 3.7.5 SUBSYSTEM DATA STRUCTURES

Data will be transmitted between the phone and device using Bluetooth serial.

### 3.7.6 SUBSYSTEM DATA PROCESSING

Bluetooth serial data will process JSON data between the app and the ESP-32

### 3.8 LCD SCREEN

The LCD screen is used to display either the current time or the name of your plant along with different screens showcasing sensor data.


Figure 6: LCD Screen Subsystem Diagram

### 3.8.1 SUBSYSTEM HARDWARE

The LCD Screen of the SmartPlanter uses a 1.28 inch Round LCD Display Module 240x 240

### 3.8.2 SUBSYSTEM OPERATING SYSTEM

### 3.8.3 SUBSYSTEM SOFTWARE DEPENDENCIES

The LCD screen uses the Arduino Esp32 TFT library to display images and text on the screen.

### 3.8.4 SUBSYSTEM PROGRAMMING LANGUAGES

The code for the SmartPlanter LCD Screen was written in C.

### 3.8.5 SUBSYSTEM DATA STRUCTURES

LCD screen will receive temperature in Fahrenheit, humidity in percentage, and the rest in strings (moisture sensor, light sensor, water tank liquid sensor) from the sensor interface.

### 3.8.6 SUBSYSTEM DATA PROCESSING

The LCD displays string data retrieved from the sensor interface

### 4 USER INTERFACE SUBSYSTEMS

The user interface system or the phone application system includes subsystems of information that the user is able to observe such as their account or functional subsystems where the user can perform actions such as adding a plant. The layer may seem that it may not have that many subsystems but the purpose of the application layer is for the user to just setup their pot and use the application to be able to see information about it whenever they want.

### 4.1 LAYER HARDWARE

This layer is purely software the only requirement is to have a mobile device does not matter what type of operating system. Further specifics of the operating system are discussed below.

### 4.2 LAYER OPERATING SYSTEM

Since we are using Flutter to develop our user interface it is compatible with multiple operating systems such as android, iOS, Windows and mac OS. Since we are building a mobile app the supported platforms for this layer are android 4.1 and above and iOS 11 and above anything below that Flutter will not be able to run on the OS.

### 4.3 LAYER SOFTWARE DEPENDENCIES

This user interface layer depends entirely on the flutter framework and Dart programming language. Make connection using library of non-sequel database (MongoDB Database) mongo_dart version (0.5.1).

### 4.4 NEW DEVICE SUBSYSTEM

The new device subsystem allows the user to connect to the smart plant pot via bluetooth. Once the connection with bluetooth is establishes, the New Device interface relays WIFI credentials through bluetooth and receives the mac address of the plant.

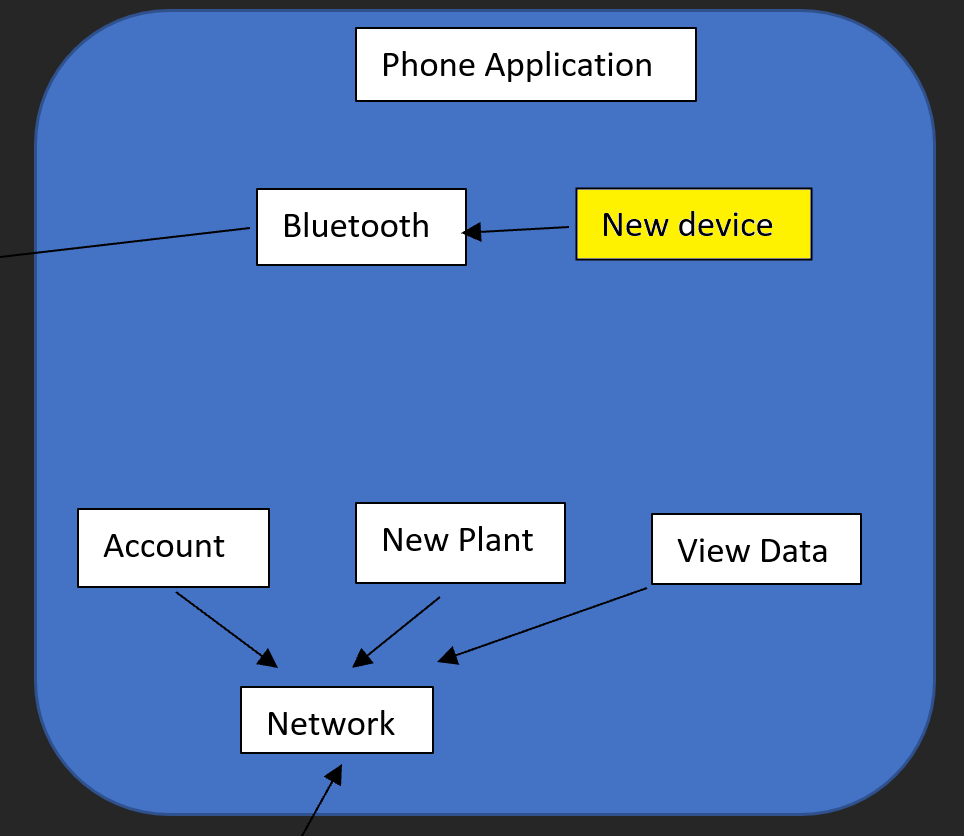
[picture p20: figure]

Figure 7: New Device Subsystem Diagram

### 4.4.1 SUBSYSTEM SOFTWARE DEPENDENCIES

Since this subsystem is used to connect the device to the network it requires the flutter_blue version 0.8.0 package.

### 4.4.2 SUBSYSTEM DATA STRUCTURES

Data sent through bluetooth from the new device interface consist of wifi credentials encoded in JSON. The MAC address returning from bluetooth will also be in JSON.

### 4.4.3 SUBSYSTEM DATA PROCESSING

Data sent and received from the bluetooth interface will be serialized/unserialized in JSON in the new device interface.

### 4.5 BLUETOOTH SUBSYSTEM

The bluetooth subsystem works as a bridge by establishing a connection used to connect the phone application’s new device interface and the smart planter hardware bluetoot.

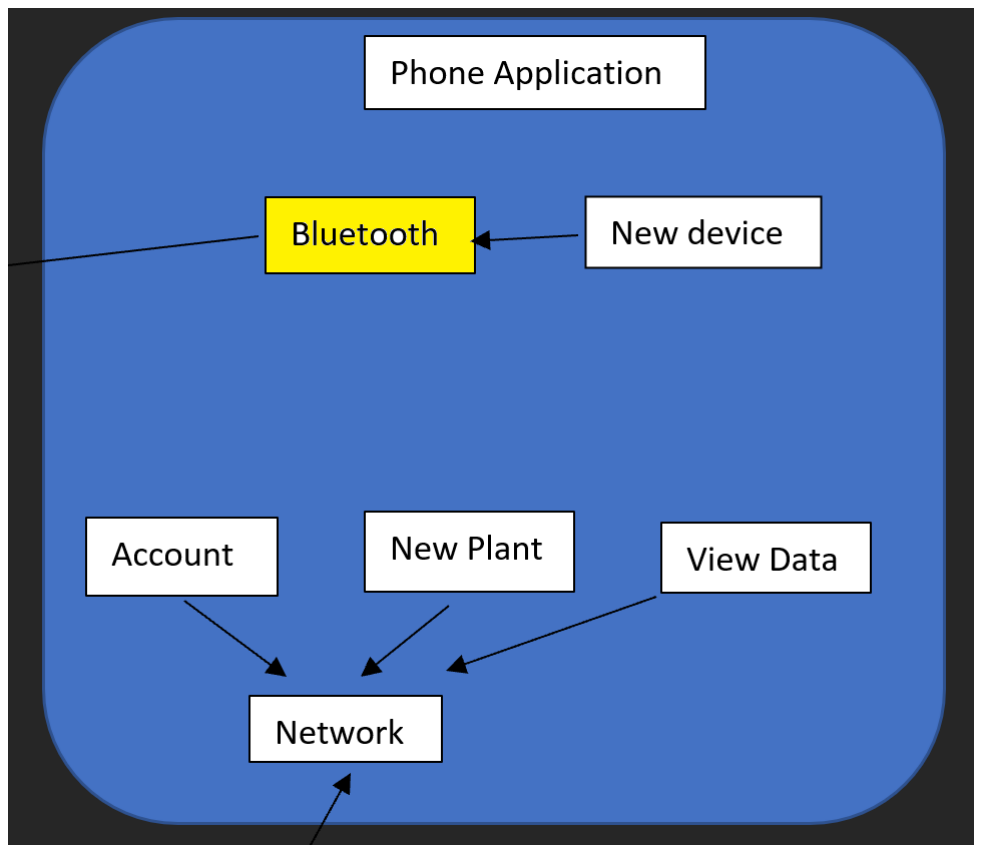
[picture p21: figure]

Figure 8: Bluetooth Subsystem Diagram

### 4.5.1 SUBSYSTEM OPERATING SYSTEM

For both iOS and Android we need permissions to use Bluetooth and access location

### 4.5.2 SUBSYSTEM SOFTWARE DEPENDENCIES

The package flutter_blue version 0.8.0 should be imported in order to implement Bluetooth within the application. flutter_blue is only compatible from version 19 of android SDK.

### 4.5.3 SUBSYSTEM DATA STRUCTURES

Data structures passed through the Bluetooth serial interface will be serialized JSON data.

### 4.5.4 SUBSYSTEM DATA PROCESSING

No data processing

### 4.6 VIEW DATA SUBSYSTEM

The purpose of the view data subsystem is only for the user to observe sensor readings with pots it has, also has additional functionality such as deleting a pot. The sensor readings will be read from the database in time intervals and display them to the user.

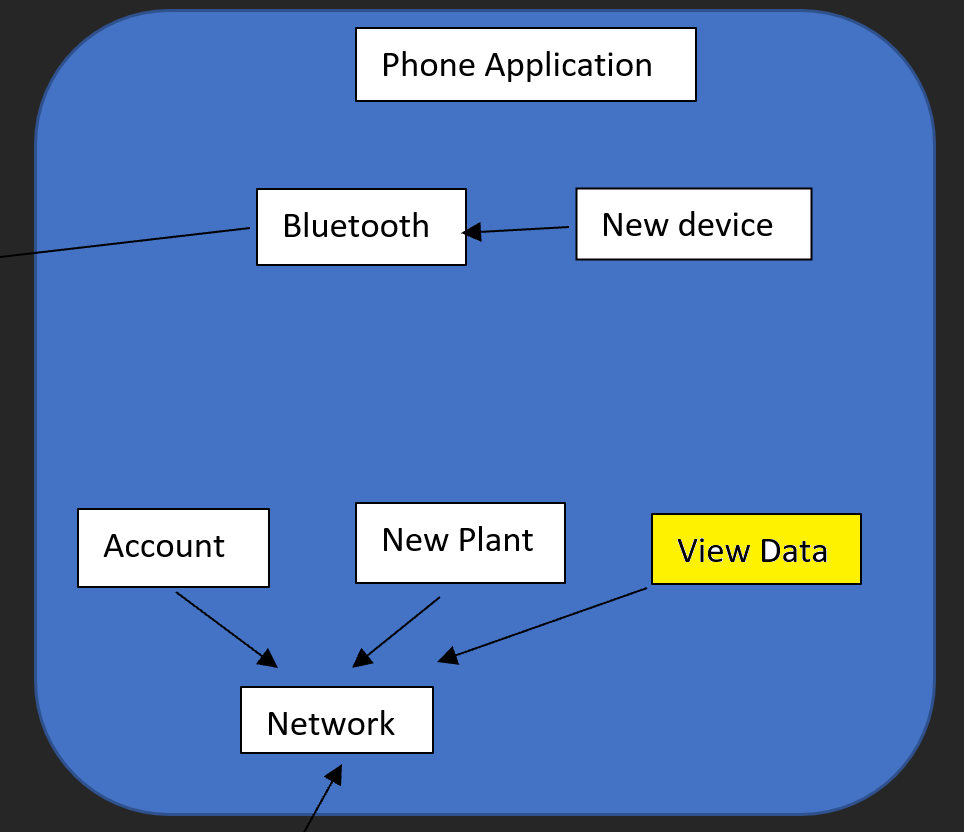
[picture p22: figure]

Figure 9: View Data Subsystem Diagram

### 4.6.1 SUBSYSTEM SOFTWARE DEPENDENCIES

The package flutter/material.dart is a dependency in order to create the UI for the view data page. View data also depends on database connection which is done by interacting with the network to pull data.

### 4.6.2 SUBSYSTEM PROGRAMMING LANGUAGES

The user interface is being done with the flutter framework.

### 4.6.3 SUBSYSTEM DATA STRUCTURES

View data interface receives data from the database through a network connection. Data received as strings.

### 4.6.4 SUBSYSTEM DATA PROCESSING

String data from the network is displayed on the view data user interface.

### 4.7 NEW PLANT SUBSYSTEM

The new plant subsystem is a component that will allow the user to edit the plant that is assigned to the smart planter instance. This works by retrieving plant classes from the database through the network connection and displaying them on the UI. When the user selects add new plant to database, the class they retrieved is pushed on to their database account in the section for their corresponding plant pot.

### 4.7.1 SUBSYSTEM SOFTWARE DEPENDENCIES

The package flutter/material.dart is a dependency in order to create the UI for the new plant page. New plant also depends on a database connection to the cloud in order to edit plant settings

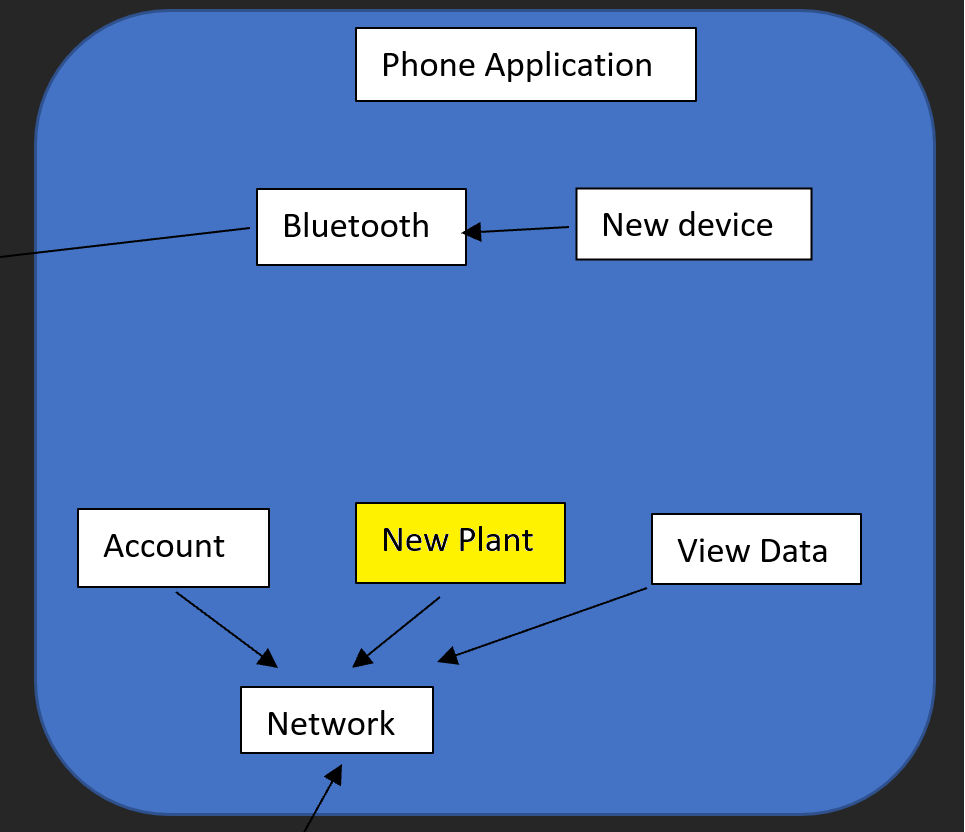
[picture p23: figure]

Figure 10: New Plant Subsystem Diagram

### 4.7.2 SUBSYSTEM PROGRAMMING LANGUAGES

The user interface is being done with the flutter framework.

### 4.7.3 SUBSYSTEM DATA STRUCTURES

Plants information send and received as classes

### 4.7.4 SUBSYSTEM DATA PROCESSING

Data sent and received through the network as classes

### 4.8 ACCOUNT SUBSYSTEM

The account subsystem allows the user to change any settings they are allowed and also view any account information.

### 4.8.1 SUBSYSTEM PROGRAMMING LANGUAGES

The user interface is being done with the flutter framework.

### 4.8.2 SUBSYSTEM SOFTWARE DEPENDENCIES

The package flutter/material.dart is a dependency in order to create the UI for the new plant page. Depends on database connection.

### 4.8.3 SUBSYSTEM DATA STRUCTURES

Data send and received in flutter string

### 4.8.4 SUBSYSTEM DATA PROCESSING

Data retrieved from the database is displayed on the UI as strings, and data sent to the database when the user changes the information is saved as a database entry string

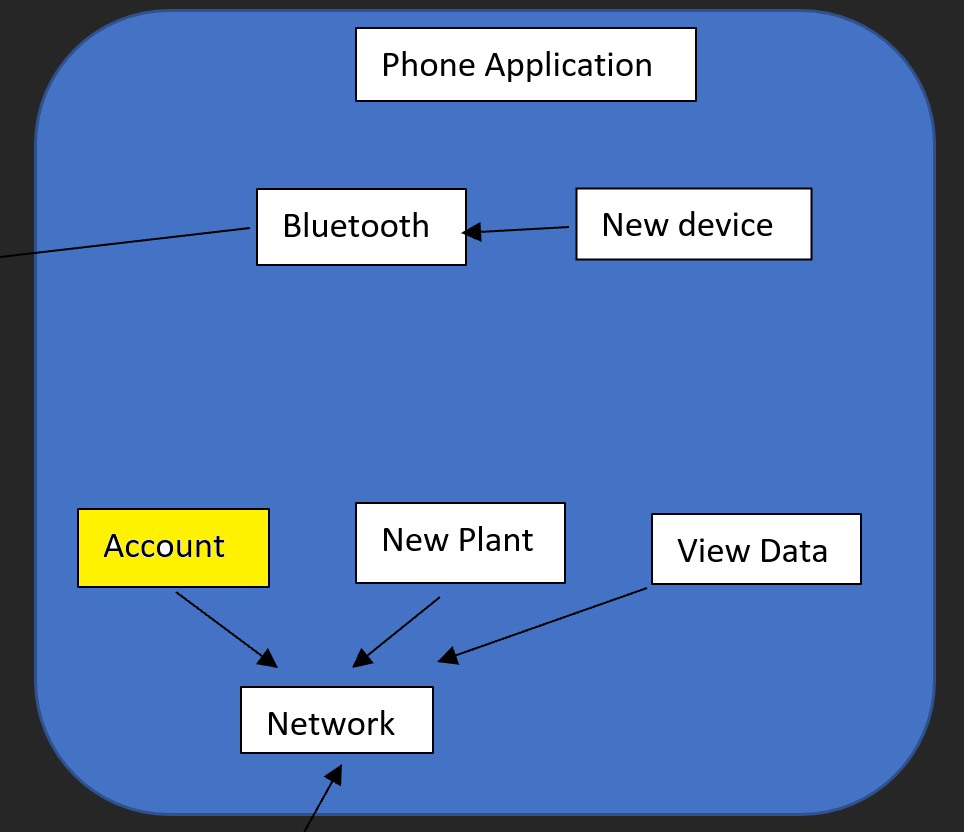
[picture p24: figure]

Figure 11: Account Subsystem Diagram

### 4.9 NETWORK SUBSYSTEM

The network is in charge of the communication between the non-SQL database(MongoDB Database), SmartPlanter application(Mobile Application) and the SmartPlanter system(Smart Planter Pot). This layer is automated system which means that its a virtual representation of the network connection between mobile application and smart planter using their WiFi and Bluetooth connection that connects to internet and update the database.

### 4.9.1 SUBSYSTEM PROGRAMMING LANGUAGES

Realm is implemented in dart

### 4.9.2 SUBSYSTEM SOFTWARE DEPENDENCIES

MongoDB with Atlas Device Sync and Realm

### 4.9.3 SUBSYSTEM DATA STRUCTURES

Have to create Object Schemas in dart to let Realm know the structure of the data being sent.

### 4.9.4 SUBSYSTEM DATA PROCESSING

Realm uses Atlas Device Sync to synchronize data between MongoDB and the phone application.

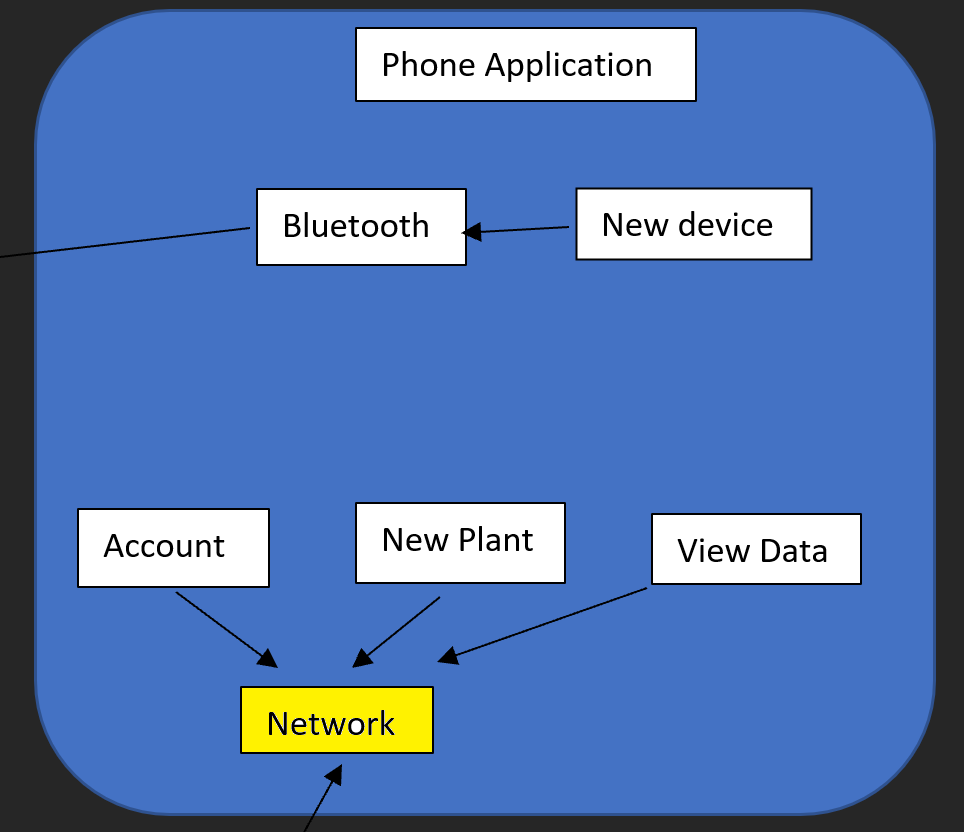
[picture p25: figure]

Figure 12: Network Subsystem Diagram

### 5 CLOUD SUBSYSTEMS

The smart planter layers is made up with network and the database, the could will communicating between the database throw the network connecting to the smart planter pot system. The smart planter pot will send data from the sensor throw the network connected to the database to be store.

### 5.1 NETWORK

The network is in charge of the communication between the non-SQL database(MongoDB Database), SmartPlanter application(Mobile Application) and the SmartPlanter system(Smart Planter Pot). This layer is automated system which means that its a virtual representation of the network connection between mobile application and smart planter using their WiFi and Bluetooth connection that connects to internet and update the database.

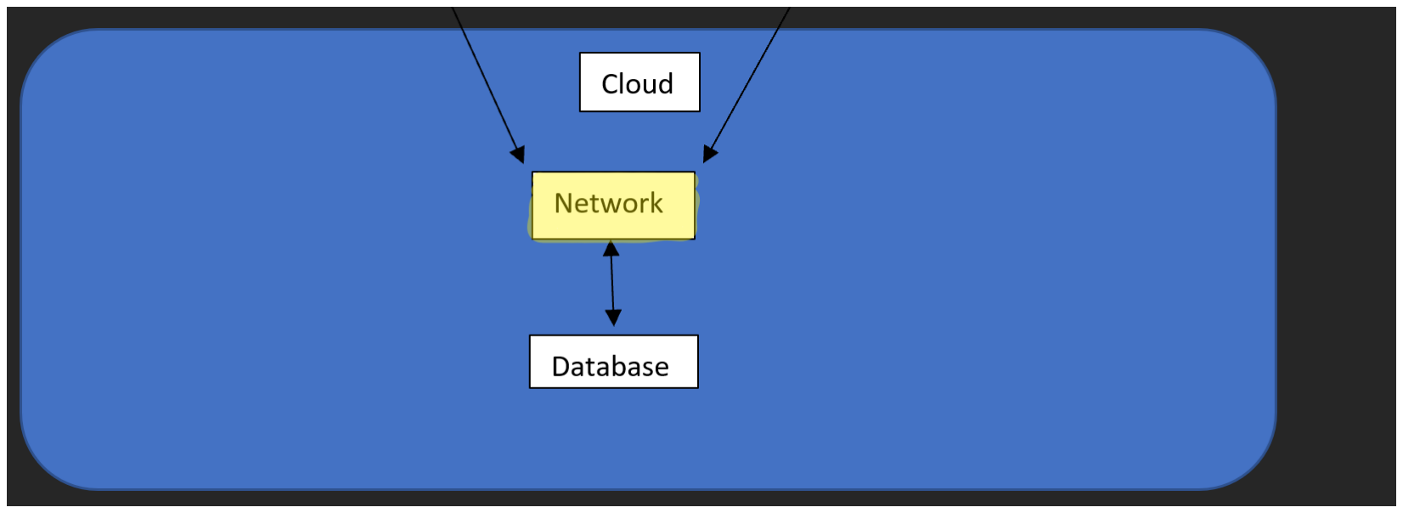
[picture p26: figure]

Figure 13: Network Subsystem Diagram

### 5.1.1 SUBSYSTEM PROGRAMMING LANGUAGES

Realm is implemented in dart

### 5.1.2 SUBSYSTEM SOFTWARE DEPENDENCIES

MongoDB with Atlas Device Sync and Realm

### 5.1.3 SUBSYSTEM DATA STRUCTURES

Have to create Object Schemas in dart to let Realm know the structure of the data being sent MongoDB will also create the same schemas to update data in the collections with that same format.

### 5.1.4 SUBSYSTEM DATA PROCESSING

ealm uses Atlas Device Sync to synchronize data between MongoDB and the phone application.

### 5.2 DATABASE

The cloud database is server-less. It needs no version control. Cloud database stores user information and plant information.


Figure 14: Database Subsystem Diagram

### 5.2.1 SUBSYSTEM PROGRAMMING LANGUAGES

MongoDB is an Open Source database written in C++. But the database is automated and supports multiple programming languages. To implement realm you can use the dart programming language.

### 5.2.2 SUBSYSTEM SOFTWARE DEPENDENCIES

MongoDB and Realm are needed in this subsystem in order to transfer data.

### 5.2.3 SUBSYSTEM DATA STRUCTURES

MongoDB offers a Document oriented storage, It is support dart programming languages and its library which can help storing data in collections even without defining the structure you can create a collections. MongoDB supports neither joins nor transactions. However, MongoDB does provide atomic operations on a single document.

### 5.2.4 SUBSYSTEM DATA PROCESSING

MongoDB supports rich query to fetch data from the database, replacing an entire document (database) or some specific fields with it’s update() command, replacing an entire document (database) or some specific fields with it’s update() command.

### 6 APPENDIX A

Include any additional documents (CAD design, circuit schematics, etc) as an appendix as necessary.

REFERENCES

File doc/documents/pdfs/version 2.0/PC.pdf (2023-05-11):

## DEPARTMENT OF COMPUTER SCIENCE & ENGINEERING

## THE UNIVERSITY OF TEXAS AT ARLINGTON

## PROJECT CHARTER

# CSE 4317: SENIOR DESIGN II SPRING 2023


## PLANT WAYS

## SMART PLANTER

SAMUEL RUIZ
KEVIN EDUARDO FLORES
LUIS GUILLERMO JAEN
DON DUI
SAMRAT BARAL
Plant Ways - Spring 2023 | page 1 of 15

REVISION HISTORY

Revision | Date | Author(s) | Description
0.1 | 09.16.2022 | SR,KF,SB,LJ,DB | Document Creation
1.0 | 12.14.2022 | SR,KF,SB,LJ,DB | Document Update
2.0 | 05.10.2023 | SR,KF,SB,LJ,DB | Final Version

CONTENTS

1 Problem Statement | 6
2 Methodology | 6
3 Value Proposition | 6
4 Development Milestones | 6
5 Background | 7
6 Related Work | 7
7 System Overview | 8
8 Roles & Responsibilities | 9
9 Cost Proposal | 9
10 Facilities & Equipment | 10
11 Assumptions | 11
12 Constraints | 11
13 Risks | 11
14 Documentation & Reporting | 11

LIST OF FIGURES

1 | Components for hardware and software | | 8
2 | Example sprint burn down chart | | 13

### 1 PROBLEM STATEMENT

Plant maintenance is a common issue in today’s households. Most people do not have the time to water their plants and some often forget. Modern plant pots have added features like moisture sensors, temperature sensors and even displays that indicate when the plant needs to be watered. However, there has not been a single pot that combines all these features with home automation.

### 2 METHODOLOGY

We are going to build a self-watering plant pot, removing the consistent maintenance required in watering a house plant on your own. This pot is called the Smart Planter. The Smart Planter will measure humidity, temperature, and light exposure. We will also build an application to interface with the planter, to customize the settings for the individual plant.

### 3 VALUE PROPOSITION

Having a SmartPlanter will help homeowners decorate their homes with plants without worrying about the maintenance or pots with no loose wiring like related home projects. SmartPlanter can also be used as a learning tool for beginners as our application would display information about a particular plant someone would want to know about.

### 4 DEVELOPMENT MILESTONES

- Project charter first draft: September 26, 2022
- SRS: October 17, 2022
- ADS: November 7, 2022
- DDS: February 13, 2023
- Demonstration of Water Pump and Moisture Sensor: End of Sprint 3
- Demonstration of Humidity and Temperature Sensor: End of Sprint 4
- Demonstration of Light Sensor: Beginning of Spring Semester
- Demonstration of Application: End of Sprint 6 (March)
- Demonstration of LCD Screen: Beginning of Sprint 7
- Demonstration of Bluetooth Connectivity: Beginning of Sprint 8
- Demonstration of Wi-Fi Connectivity: End of Sprint 8
- Demonstration of 3D Design Pot: End of Sprint 8
- COE Innovation Day Poster: April 18, 2023
- Final Project Demonstration: May 5, 2023

### 5 BACKGROUND

The smart planter will solve many of the problems when it comes to doing maintenance on plants. People who have plants sitting in their house tend to forget or have a busy work schedule to take care of the plant. Therefore, the plant ends up dying, so the smart planter could be used by people who like having plants around them but do not like to take care of the plant often.

The smart planter application can also be used as a learning tool for people who do not know anything about taking care of plants and want to learn how to take care of their plant by utilizing a cloud database which obtains information about the plant. For instance, some might not know how often to water a plant, so they sometimes over-water or under-water a plant, causing harmful deficiencies, which can lead to the death of the plant. Additionally, new plant caretakers could unknowingly keep their plant in an environment that’s too warm or cold for that specific species, or too dark/bright for the plant, which can also be harmful. The smart planter’s automation would remove these issues and ensure the longevity of the users plant. The smart planter cloud database will have information about different plants, the user can pick the type of plant they are planting in the smart planter, and they can send a request to the site for new plants to add to the list. The smart planter is designed to be used in a regular household, but can also be retooled to use in a small commercial setting to grow plants on a small scale in a green house.

The purpose of the smart planter is to be affordable and decorative to the public. There are some IoT planters out there, but they are expensive or have a self-watering system outside of the pot. The smart planter is supposed to combine the self-watering and IoT pot in one for ease of use.

### 6 RELATED WORK

- Indoor Herb Garden Kit and Refills [1] The Click Grow is a commercially available smart planter where a device grows plants by watering them automatically its cheapest device is about $100. The difference between this product and our smart planter is that we will implement an LCD screen and the user will be able to interface with the pot via a phone through an application.
- Lua, the smart planter with feelings! [4]

The Lua smart planter is a campaign, that is now closed, on Indiegogo which is a crowdfunding platform. The Lua smart planter will not work the same as our planter for customers because the Lua planter just tells you how the plant is âfeelingâ through an animated screen while ours will be watered automatically, the user only needs to refill the tank. Also, the Lua doesnât have an application so there is no way to interface with the pot that displays specific information.

- Smart Garden with IoT Plant Monitoring System [5]

Bolt IoT gives instructions to people for them to create their own IoT devices and they specify how people can create a smart planter. Even though people creating their own project may be cheaper this project is not as aesthetically pleasing as our planter since there are wires everywhere. Lastly, it has a text messaging system to send information about the plant instead of an application.

- Smart Garden Planter 1-Unit Pot [2]

LetPot sells a self-watering pot but the difference between theirs and ours is that they do not use a motor to administer water to the plant but have the bottom of the pot touching the water tank to soak the water in. Also, the pot doesnât come with any sensors or an application, so the user has no way to monitor information about the plant.

- Amazon.com : Self Watering Pots for Indoor Plants [3]

This self-watering pot by ETGLCOZY that is commercially available through Amazon is somewhat related to what we want to create but it is missing a couple of features. This pot may be cheaper, but we will have an LCD screen on our pot and have the pot connected to our mobile application for customers to be able to monitor and learn more about their plant.

### 7 SYSTEM OVERVIEW


Figure 1: Components for hardware and software

The Smart Planter’s physical build includes a tank filled with water which will be used to water the soil, a pump which will water the soil automatically (depending on the instructions how it receives the data), and It will also have an LCD screen attached which will showcase a clock with the current time. There will also be a metal mesh between the bottom of the plant’s soil and the drainage water channel, which is leading directly toward the water tank. Additionally, the cable systems and sensitive electronic modules will be insulated and protected within separate layer section inside the pot.

The Smart Planter will be monitored and controlled by an app with the following functionalities: searching for the desired plant’s information from the cloud database, which includes the humidity percentage, required temperature, and light exposure needed, along with the plants actual picture and its name, sending the specific plant’s data over to the pot’s local memory storage, and monitoring the current status of the plantâs humidity, temperature, and light exposure.

The app will initially connect with the Smart Planter via Bluetooth. Then the Bluetooth connection will be disconnected and then overridden by a WIFI connection between the mobile/website app and Smart Planter. The app should request the required data as well as the instructions from a cloud-based server, then send it over to the Smart Planter. The Smart Planter will then follow the instructions and water the plant accordingly. The Smart Planter mobile/website application is capable of monitoring multiple smart pots from a single user account.

### 8 ROLES & RESPONSIBILITIES

The stakeholders for this project are everyone on our team, Professor Gieser, and the University of Texas at Arlington for sponsoring our project.

There is currently no contact for the customer side since this is a student pitched project. The team will contact Professor Gieser in the case that anything is needed from the University and all documentation will be submitted to him.

Everyone on the team will act as a product owner and agree to any changes made to the project scope.

The responsibilities of each team member are as follows:

- Samuel J. Ruiz Hardware Development and Embedded Systems Programming

Printed Circuit Board Design

- Kevin Eduardo Flores Hardware development and programming
- Luis Guillermo Jaen

Android application development and UX/UI design

- Don Dui

Hardware development and programming

- Samrat Baral

Hardware development and programming

### 9 COST PROPOSAL

The project will have require the hardware mentioned in the system overviews. The project estimate is about $100.00 for each prototype on actuators and sensors and other required hardware if we make gallon size without any software cost.
An Arduino Uno will also be purchased for learning purposes along with a breadboard. The estimated cost will be $28.50 for the Arduino Uno and $9.99 for the breadboard kit.
Once the first prototype is complete, the team will research a variety of plants and soil to test the product with. The cost analysis for this section will be updated in a future project charter revision.

### 9.1 PRELIMINARY BUDGET

### 9.2 CURRENT & PENDING SUPPORT

The only funding for this project is the $800 budget given to the team from the University of Texas at Arlington CSE department. All items purchased from this budget will be returned to the UTA CSE department.

Component Name | Quantity | Cost
Humidity and Temperature Sensor x5 | 1 | $10.29
Photo-resistor Pack of 20pcs | 1 | $6.68
Soil Moisture Sensor Module x5 | 1 | $9.99
IRLB8721 MOSFET Transistors x10 | 1 | $10.99
Micro Submersible Mini Water Pump x 4 | 2 | $22.78
ESP32 ESP-WROOM-32 Development Board x3 | 2 | $37.76

Table 1: Overview of hardware component parts and cost

Any team member who wishes to keep a prototype for themselves will have to build it out of parts purchased from their own budget.

### 10 FACILITIES & EQUIPMENT

For the documentation of this project, the team will be meeting in the 2nd floor of the UTA library. This workspace contains whiteboards and open spaces good for discussing ideas and changes to the project scope.

For the software elements, the team will meet in the designated spot assigned by the professor in room 208 of the Engineering Research Building.

For the hardware elements,the team will request access to the Nedderman Hall Computer Engineering lab. This lab contains majority of the following necessary equipment:

Soldering Station
3D Printer
Workstations

The team will also get together with Professor Gieser next semester to discuss ways of outsourcing the construction of the Printed Circuit Boards and find potential software applications we can use to 3D design our smart planter.

Some other equipment we will require are multi-meters to read voltages and currents in our setup. Sam and Kevin own multi-meters which those can be used during our meetings. We also require an Arduino kit that contains an Arduino micro-controller, jumper cables and breadboards. Sam and Don own a kit which they can use when working on the hardware aspect of the project, anyone wanting to participate in hardware tasks can purchase a kit online. In order to program our hardware we need to use the Arduino IDE which is open source. We will require the Flutter framework for our mobile application which is also open source. Additional equipment that we will purchase personally for our pot are temperature, humidity, light, moisture and water level sensors. Additionally we will acquire a LCD screen, a water pump motor and a regular pot for our prototype. Any additional hardware needed such as resistors, diodes, relays, etc. will be purchased as needed since we may or may not require them.

### 11 ASSUMPTIONS

The following list contains critical assumptions related to the implementation and testing of the project.

- The purchased hardware will not arrive damaged and will not fail when testing prototype
- The team will have a suitable lab area to begin working on the electronic components by sprint 3
- UTA network will allow for the ESP-32 to connect through WIFI
- All necessary components will be available on Amazon and should arrive by sprint 3
- Software application will be available to install from GitHub or Android app-store by final demonstration

### 12 CONSTRAINTS

The following list contains key constraints related to the implementation and testing of the project.

- Final Prototype demonstration will be complete by May 1st, 2023
- Total development cost must not exceed $800.
- The final prototype must keep the plant alive in a healthy environment
- Final prototype must follow the National Electrical code for wiring
- Software applications must protect the userâs private information.

### 13 RISKS

This section should contain a list of at least 5 of the most critical risks related to your project. Additionally, the probability of occurrence, size of loss, and risk exposure should be listed. For size of loss, express units as the number of days by which the project schedule would be delayed. For risk exposure, multiply the size of loss by the probability of occurrence to obtain the exposure in days. For example: The following high-level risk census contains identified project risks with the highest exposure. Mitigation strategies will be discussed in future planning sessions.

Risk description | Probability | Loss (days) | Exposure (days)
Delays in shipping from overseas vendors | 0.10 | 15 | 1.5
Availability of affordable LCD screens due to shortages | 0.20 | 10 | 2
Receiving faulty parts and needing to reorder more | 0.10 | 7 | 0.7
Failure to connect device through UTA network | 0.30 | 14 | 2
Failed acquisition of special 3D printing filament, due to low supply | 0.10 | 10 | 1

Table 2: Overview of highest exposure project risks

### 14 DOCUMENTATION & REPORTING

### 14.1 MAJOR DOCUMENTATION DELIVERABLES

### 14.1.1 PROJECT CHARTER

This document will be maintained using overleaf and will need to be updated if any changes are needed. The initial version will be delivered September 26th and the final version is estimated to be released in the Spring 2023 semester once all changes are finalized.

### 14.1.2 SYSTEM REQUIREMENTS SPECIFICATION

The System Requirements Specification document will also be maintained using overleaf. The initial version will be released October 17th, 2022, and all changes will be finalized around the Spring 2023 semester.

### 14.1.3 ARCHITECTURAL DESIGN SPECIFICATION

The Architecture Design Specification document will also be maintained using overleaf. The initial version will be released November 7th, 2022 and all changes finalized around the Spring 2023 semester.

### 14.1.4 DETAILED DESIGN SPECIFICATION

The Architecture Design Specification document will also be maintained using overleaf. The initial version will be released and finalized on February 13th, 2023 semester.

### 14.2 RECURRING SPRINT ITEMS

### 14.2.1 PRODUCT BACKLOG

The items added to the backlog will be decided upon a group vote. The group will decide the priority of the items depending on the level of difficulty and time consumption. We will be using Trello software to share the product backlog.

### 14.2.2 SPRINT PLANNING

Sprint planning meetings will be held every other Friday to determine the requirements of the next sprint. There will be a total of 4 sprints this semester.

### 14.2.3 SPRINT GOAL

The group will decide what the sprint goal is by vote. There are currently no customers involved as this is a student pitch project by Sam Ruiz.

### 14.2.4 SPRINT BACKLOG

The group will decide on the sprint backlog by considering the time constraints and dependencies of other backlog items.

### 14.2.5 TASK BREAKDOWN

Backlog tasks will be decided by each team member volunteering to take on the task of their choosing. Time spent on those tasks will be recorded in the team members’ engineering notebook and then on the sprint breakdown.

### 14.2.6 SPRINT BURN DOWN CHARTS

Kevin will be in charge of generating the burndown charts for each sprint. The amount of effort expended by each individual team member will be discussed during the weekly meetings. The burndown chart will follow the format created in Excel.

### 14.2.7 SPRINT RETROSPECTIVE

Sprint Retrospective meetings will be held every other Friday. The team will determine the status of the previous sprints and discuss any changes that need to be considered before the next sprint planning meeting.


Figure 2: Example sprint burn down chart

### 14.2.8 INDIVIDUAL STATUS REPORTS

Each team member will complete tasks that are assigned to them, contributing to the teamâs burnout chart. The individual status reports will be completed by the individual team members and submitted to Professor Gieser.

### 14.2.9 ENGINEERING NOTEBOOKS

Each team member will be required to complete at least one page of the engineering notebook every sprint. They will keep a detailed account of their progress along with details of how long they spent working that sprint.

### 14.3 CLOSEOUT MATERIALS

### 14.3.1 SYSTEM PROTOTYPE

The system prototype will be a 3D printed plant pot. It will be demonstrated during the senior design demo by using the prototype and a demo video.

### 14.3.2 PROJECT POSTER

The project poster will be a 3x5 poster board. It will be delivered during the senior design demo.

### 14.3.3 WEB PAGE

The project poster will be a 3x5 poster board. It will be delivered during the senior design demo.

### 14.3.4 DEMO VIDEO

The demo video will be about a minute long video showcasing the SmartPlanter along with instructions on the initial setup.

### 14.3.5 SOURCE CODE

The source code will be maintained on a GitHub repository. New branches will be created for each section of the software and will be merged during a group code review.

### 14.3.6 SOURCE CODE DOCUMENTATION

GitHub repository will include a README file for documentation.

### 14.3.7 HARDWARE SCHEMATICS

The project will include a custom PCB layout. The wiring diagram will be added in the future semester once the layout has been designed.

### 14.3.8 CAD FILES

The SmartPlanter pot will use a custom 3D design. The CAD files will be provided in a GitHub repository at the end of the Spring 2023 semester.

### 14.3.9 INSTALLATION SCRIPTS

The planter will include the code necessary to run. The phone application will be included in GitHub for Android phones to install.

REFERENCES

[1] Indoor herb garden kit and refills.
[2] Self-watering pot with 21 days watering-freeï¼1-unit potï¼letpot self-watering smart planter.
[3] self watering pots for indoor plants.
[4] Vivien Muller. Lua, the smart planter with feelings!, Jun 2019.
[5] Pranav Pai Vernekar. Smart garden with iot plant monitoring system.

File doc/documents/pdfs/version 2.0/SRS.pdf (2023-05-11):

## DEPARTMENT OF COMPUTER SCIENCE & ENGINEERING

## THE UNIVERSITY OF TEXAS AT ARLINGTON

## SYSTEM REQUIREMENTS SPECIFICATION

# CSE 4317: SENIOR DESIGN II SPRING 2023


## PLANT WAYS

## SMART PLANTER

SAMUEL RUIZ
KEVIN FLORES
DON BUI
LUIS JAEN
SAMRAT BARAL
Plant Ways - Spring 2023 | page 1 of 26

REVISION HISTORY

Revision | Date | Author(s) | Description
0.1 | 10.07.2022 | SR,KF,LJ,DB,SB | Document Creation
1.0 | 10.17.2022 | SR,KF,LJ,DB,SB | Document Draft
2.0 | 5.10.2023 | SR,KF,LJ,DB,SB | Final Version

CONTENTS

1 Product Concept | 9
2 Product Description | 10
3 Customer Requirements | 12

4 Packaging Requirements | 17
5 Performance Requirements | 18

6 Safety Requirements | 19
7 Security Requirements | 20
8 Maintenance & Support Requirements | 21

9 Other Requirements | 23
10 Future Items | 24

LIST OF FIGURES

1 | Components of Smart Planter (Hardware and Software) | | 9
2 | Screen conceptual design | | 11

### 1 PRODUCT CONCEPT

The product targets plant beginners and people who neglect plant care. Its purpose is to be used as a learning tool and to automate plant care. The sensors system collects data and users would be able to read in data via mobile application. The mobile apps purpose is ease of use of monitoring the plant.

### 1.1 PURPOSE AND USE

Our product is intended to be left on its own since the plant care is automated and should only be refilled with water periodically. Users can see information about the plant through the application.

### 1.2 INTENDED AUDIENCE

This product is made for people who like to have plants around their home, but have trouble keeping up with the maintenance. For instance, housewives or househusbands would benefit from this since it would alleviate some of their routine house work, allowing them to focus more on other tasks. College students who are busy with lots of school work would find our product useful as well. The middle-class and above are the classes which this product is geared towards. The Smart Planter is intended for general use, since the system is mostly automated, it’s not that complex.


Figure 1: Components of Smart Planter (Hardware and Software)

### 2 PRODUCT DESCRIPTION

This section provides the reader with an overview of the Smart Planter. The primary operational aspects of the product, from the perspective of end users, maintainers and administrators, are defined here. The key features and functions found in the product, as well as critical user interactions and user interfaces are described in detail.

### 2.1 FEATURES & FUNCTIONS

The smart planter will take care of the plant by automatic watering the plant. The smart planter will have a sensor that takes in data of how much sun light the plant is getting. The smart planter has a moisture sensor that will instruct when the water pump should turn on, and water the plant when the soil is too dry. The smart planter will have a temperature sensor and it will be use for gathering the air temperature data, and the smart planter will have humidity sensor which will be use to gather the humidity percentage of the surrounding area. The smart planter pot will have a screen that will display the name of the plant or the time on the screen. All the gathered data will store on a data base, which could be accessed though the app, and the app will be connected by WiFi. The smart planter should almost look like a regular planting pot with a screen in front of the pot displaying the name of plant or the time on it.

### 2.2 EXTERNAL INPUTS & OUTPUTS


### 2.3 PRODUCT INTERFACES

The app will have an account the user logs into, and it will hold all the smart planter pots that the user has registered with app. There is a button the in the app that the user could use to add more smart planters to the account. There is also an account button in the app that lets the user see the user information. The home button will let the user go to the home dashboard.


Figure 2: Screen conceptual design

### 3 CUSTOMER REQUIREMENTS

The SmartPlanter was a student pitched project by Samuel Ruiz. The customer requirements were selected by a group consensus from all the members of the PlantWays team.

### 3.1 PLANT MONITORING

### 3.1.1 DESCRIPTION

The Smart Planter should be able to monitor the plants’ environmental conditions through sensors. This includes humidity, temperature, soil moisture and light exposure.

### 3.1.2 SOURCE

Student pitched CSE Senior Design project specifications by group member Samuel Ruiz

### 3.1.3 CONSTRAINTS

Sensors have the possibility of wear and tear which may require customers to get replacements.

### 3.1.4 STANDARDS

We will be using the NEC wire color coding standards.

### 3.1.5 PRIORITY

Critical (must have or product is a failure)

### 3.2 PLANT POT

### 3.2.1 DESCRIPTION

The plant pot will be a 3D print design incorporating all the circuitry inside and will be the ideal shape of a regular pot. The design must include designated section to install the plant sensors such as: soil moisture sensor, light sensor, water pump, temperature, humidity sensor, and water tank water level sensor. In addition to these sensors, the design must also include a refillable water tank, a hole for the USB cable, and a button to enable/reset device paring.

### 3.2.2 SOURCE

Student pitched CSE Senior Design project specifications by group member Samuel Ruiz

### 3.2.3 CONSTRAINTS

The plant pot design must keep an ideal environment for an indoor plant while taking into drainage into consideration by either ventilation or reusing the water with a filter. The light sensor must be placed in the design in an ideal position where the plant is not covering sunlight.

### 3.2.4 STANDARDS

We will be using the NEC wire color coding standards.

### 3.2.5 PRIORITY

Critical (must have or product is a failure)

### 3.3 LCD SCREEN

### 3.3.1 DESCRIPTION

The design of the plant pot will have an LCD screen in the front that must include the local time, low water tank notification, and a possible slideshow of sensor data.

### 3.3.2 CONSTRAINTS

The LCD screen must not draw more power than needed to complete the main functions of the Smart-Planter

### 3.3.3 STANDARDS

We will be using the NEC wire color coding standards.

### 3.3.4 SOURCE

Student pitched CSE Senior Design project specifications by group member Samuel Ruiz

### 3.3.5 PRIORITY

Critical (must have or product is a failure)

### 3.4 SELF WATERING SYSTEM

### 3.4.1 DESCRIPTION

The SmartPlanter must be self watering. The water pump must activate when the soil moisture indicated the plant needs water and will stop once the sensor indicates the ideal soil moisture is met. The soil moisture parameters can be selected through the mobile application.

### 3.4.2 SOURCE

Student pitched CSE Senior Design project specifications by group member Samuel Ruiz

### 3.4.3 CONSTRAINTS

The self watering system should take into account the time of day for watering the plant. Watering the plant in the evenings can cause rot in the plants. The self watering system must be disabled when the water tank is low to prevent damage to the water pump.

### 3.4.4 STANDARDS

We will be using the NEC wire color coding standards.

### 3.4.5 PRIORITY

Critical (must have or product is a failure)

### 3.5 MOBILE PHONE APPLICATION

### 3.5.1 DESCRIPTION

The SmartPlanter will include a mobile phone application that the user can download and install. The phone application must include a user account creation section before the user is allowed to connect their device.

### 3.5.2 SOURCE

Student pitched CSE Senior Design project specifications by group member Samuel Ruiz

### 3.5.3 CONSTRAINTS

User information must be stored in a secure server. The user account must be password protected and user data will never be shared to respect user privacy.

### 3.5.4 STANDARDS

SB-327 Information Privacy: Connected Devices
Device will be equipped with reasonable security features for IoT devices.

### 3.5.5 PRIORITY

Critical (must have or product is a failure)

### 3.6 MOBILE PHONE APPLICATION: DEVICE CONNECTIVITY

### 3.6.1 DESCRIPTION

The SmartPlanter application must allow the users to pair to their SmartPlanter device and link the device to their local network. The button on the smart planter will allow the device to either begin or reset device pairing. Once the device is paired and set up, all the paired devices will be displayed on the home screen along with an option to Add New Plant.

### 3.6.2 SOURCE

Student pitched CSE Senior Design project specifications by group member Samuel Ruiz

### 3.6.3 CONSTRAINTS

Device pairing should simplify the process for customers not accustomed to technology.

### 3.6.4 STANDARDS

Wi-Fi is the trademark name for any Wireless Local Area Network (WLAN) that follows the IEEE 802.11 standard. It most commonly operates in the 2.4 and 5 GHz ISM Bands, but newer versions also target other frequency bands. BluetoothÂ® technology is a low-power wireless solution that operates in the 2.4 GHz ISM band.

### 3.6.5 PRIORITY

Critical (must have or product is a failure)

### 3.7 MOBILE PHONE APPLICATION: NEW PLANT

### 3.7.1 DESCRIPTION

The SmartPlanter application must allow users to add a new pot and plant to their profile, and give them names. When the user clicks on Add Smart Planter, they must be able to add a new smart planter pot to their account and name the pot, also giving the name of the type of plant they have. Once the planter is set up, the sensor data will be transmitted to the database.

### 3.7.2 SOURCE

Student pitched CSE Senior Design project specifications by group member Samuel Ruiz

### 3.7.3 CONSTRAINTS

### 3.7.4 STANDARDS

SB-327 Information Privacy: Connected Devices
Device will be equipped with reasonable security features for IoT devices.

### 3.7.5 PRIORITY

High (very important to customer acceptance, desirability)

### 3.8 MOBILE PHONE APPLICATION: CALIBRATE

### 3.8.1 DESCRIPTION

The SmartPlanter application will include a calibrate option after the device is set up. The user will place the empty plant pot in their ideal house location and select the calibrate option. The SmartPlanter will measure light exposure, temperature, and humidity once an hour for the next 24 hours. After the time is up, the application will provide the user with an average of the measured results along with a list of ideal plants for that location.

### 3.8.2 SOURCE

Student pitched CSE Senior Design project specifications by group member Samuel Ruiz

### 3.8.3 CONSTRAINTS

### 3.8.4 STANDARDS

SB-327 Information Privacy: Connected Devices
Device will be equipped with reasonable security features for IoT devices.

### 3.8.5 PRIORITY

Low (nice to have, will include if time/resource permits)

### 3.9 MOBILE PHONE APPLICATION: NOTIFICATIONS

### 3.9.1 DESCRIPTION

The SmartPlanter application should send phone notifications to the user to alert them of the following scenarios: Water tank is running low, plant is not getting enough sunlight, temperature is not ideal, or humidity is not ideal.

### 3.9.2 SOURCE

Student pitched CSE Senior Design project specifications by group member Samuel Ruiz

### 3.9.3 CONSTRAINTS

Phone application should have the ability to turn off notifications at user’s request and refrain from over notifying the user.

### 3.9.4 STANDARDS

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

### 3.9.5 PRIORITY

Low (nice to have, will include if time/resource permits)

### 3.10 SOLAR POWER

### 3.10.1 DESCRIPTION

The SmartPlanter will include a solar panel along with a battery to remove the need for wires.

### 3.10.2 SOURCE

Student pitched CSE Senior Design project specifications by group member Samuel Ruiz

### 3.10.3 CONSTRAINTS

Adding solar panels might be ideal for the smart planter but will result in constraints on the sustainability of the battery. Keeping the LCD screen on will drain deplete the battery faster and cause the device to shut down during the night.

### 3.10.4 STANDARDS

We will be using the NEC wire color coding standards.

### 3.10.5 PRIORITY

Future (not feasible in this version of the product, but should be considered for a future release)

### 4 PACKAGING REQUIREMENTS

The smart planter would be fully assembled in a box with a step by step instruction manual on how to set up the pot. The customer will need to download an application for the smart planter via app store in order to interface with the pot. The manual would also include a tech support number and a video link (showing how to set up the pot) if they are unable to set up their smart planter.

### 4.1 INSTRUCTION MANUAL

### 4.1.1 DESCRIPTION

The instruction manual will have a step by step process on how to interface with the pot via mobile application. It will also have a contact support number in case they have any trouble setting up. A video link will be provided as well in order to see how to set up the pot.

### 4.1.2 SOURCE

Samuel Ruiz

### 4.1.3 CONSTRAINTS

The customer will need WiFi in order to connect the pot to the network.

### 4.1.4 PRIORITY

Future

### 4.2 BOX PACKAGE

### 4.2.1 DESCRIPTION

The smart planter will be stored in a box with different color choices for customers and the logo of Plant Ways.

### 4.2.2 SOURCE

Samuel Ruiz

### 4.2.3 CONSTRAINTS

Smart Planter will only be limited to certain colors.

### 4.2.4 STANDARDS

ISO 55.020 Packaging and Distribution of goods in general

### 4.2.5 PRIORITY

Future

### 5 PERFORMANCE REQUIREMENTS

The SmartPlanter must include the following performance requirements to ensure an optimal user ex-perience and to reduce risk of hardware failure.

### 5.1 STOPPING THE WATER PUMP

### 5.1.1 DESCRIPTION

When the device measures ideal soil moisture or low water tank levels, the water pump must cease to pump within less than 1ms. This crucial operation must be completed within less than a second to avoid damage to the water pump.

### 5.1.2 SOURCE

Student pitched CSE Senior Design project specifications by group member Samuel Ruiz

### 5.1.3 CONSTRAINTS

The sustainability of the water pump will depend on the soil moisture sensor and water level sensor. Faulty sensor data can lead to the damage of the water pump.

### 5.1.4 STANDARDS

We will be using the NEC wire color coding standards.

### 5.1.5 PRIORITY

Critical (must have or product is a failure)

### 5.2 SEARCHING PLANT DATABASE

### 5.2.1 DESCRIPTION

Users will be able to set up their SmartPlanter but searching for their plant through a search bar. Once the correct plant is found, the sensor settings can be transmitted to the device. The speed of the search is crucial to not have customers waiting more than 30 seconds to complete their search.

### 5.2.2 SOURCE

Student pitched CSE Senior Design project specifications by group member Samuel Ruiz

### 5.2.3 CONSTRAINTS

Creating a large database of plants will increase the search time for the user. The prototype SmartPlanter will only support 2-5 house plants but the consumer version will have to support over thousands search results.

### 5.2.4 STANDARDS

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

### 5.2.5 PRIORITY

Future (not feasible in this version of the product, but should be considered for a future release)

### 6 SAFETY REQUIREMENTS

We will follow the Laboratory Equipment LOTO Procedures if we use any fabrication equipment for our project. We will also follow the NEC wiring compliance in order for the safety of the customer and to protect any electrical components.

### 6.1 LABORATORY EQUIPMENT LOCKOUT/TAGOUT (LOTO) PROCEDURES

### 6.1.1 DESCRIPTION

Any fabrication equipment provided used in the development of the project shall be used in accordance with OSHA standard LOTO procedures. Locks and tags are installed on all equipment items that present use hazards, and ONLY the course instructor or designated teaching assistants may remove a lock. All locks will be immediately replaced once the equipment is no longer in use.

### 6.1.2 SOURCE

CSE Senior Design laboratory policy

### 6.1.3 CONSTRAINTS

Equipment usage, due to lock removal policies, will be limited to availability of the course instructor and designed teaching assistants.

### 6.1.4 STANDARDS

Occupational Safety and Health Standards 1910.147 - The control of hazardous energy (lockout/tagout).

### 6.1.5 PRIORITY

Critical

### 6.2 NATIONAL ELECTRIC CODE (NEC) WIRING COMPLIANCE

### 6.2.1 DESCRIPTION

Any electrical wiring must be completed in compliance with all requirements specified in the National Electric Code. This includes wire runs, insulation, grounding, enclosures, over-current protection, and all other specifications.

### 6.2.2 SOURCE

CSE Senior Design laboratory policy

### 6.2.3 CONSTRAINTS

High voltage power sources, as defined in NFPA 70, will be avoided as much as possible in order to minimize potential hazards.

### 6.2.4 STANDARDS

NFPA 70

### 6.2.5 PRIORITY

Critical

### 7 SECURITY REQUIREMENTS

The smart planter app will have a login screen that will ask for a username and password in order to login to a specific account. Implementing a login screen will protect a users account from others users. The database will have encryption to protect the user information.

### 7.1 LOGIN SCREEN

### 7.1.1 DESCRIPTION

The smart planter app will have login screen prompting for a username and password.

### 7.1.2 SOURCE

Samuel Ruiz

### 7.1.3 CONSTRAINTS

When creating a new account, application should provide users with password requirements to ensure a level of password complexity.

### 7.1.4 STANDARDS

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

### 7.1.5 PRIORITY

Critical

### 7.2 ENCRYPTION FOR DATABASE

### 7.2.1 DESCRIPTION

Database will be encrypted in order to protect users information being leaked.

### 7.2.2 SOURCE

Samuel Ruiz

### 7.2.3 CONSTRAINTS

The limits to the security of the cloud database we service.

### 7.2.4 STANDARDS

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

### 7.2.5 PRIORITY

Future

### 8 MAINTENANCE & SUPPORT REQUIREMENTS

PlantWays will provide support for the SmartPlanter and any future products by including a department dedicated to providing customer support. This department will include developers from PlantWays and will be stationed locally in Arlington.

### 8.1 HELP DESK

### 8.1.1 DESCRIPTION

The SmartPlanter will require a help desk team to continue to provide support for the product. The help desk will include a small team of IT experts who can assist the customer with any issues with the device, identify if the issue is hardware or software related, and issue refunds/returns/repairs.

### 8.1.2 SOURCE

Student pitched CSE Senior Design project specifications by group member Samuel Ruiz

### 8.1.3 CONSTRAINTS

Help desk employees must be compensated at a reasonable hourly pay.

### 8.1.4 STANDARDS

Texas Minimum Wage Act

### 8.1.5 PRIORITY

Future

### 8.2 HARDWARE TEAM

### 8.2.1 DESCRIPTION

SmartPlanter will also include a hardware team to handle device repairs and returns due to hardware failure. Hardware team will identify any possible hardware failure and find solutions.

### 8.2.2 SOURCE

Student pitched CSE Senior Design project specifications by group member Samuel Ruiz

### 8.2.3 CONSTRAINTS

If hardware failure is due to customer then no replacements or repairs will take place.

### 8.2.4 STANDARDS

### 8.2.5 PRIORITY

Future

### 8.3 SOFTWARE TEAM

### 8.3.1 DESCRIPTION

SmartPlanter will include a software developer team to handle software related issues and updates. The software team will continue to support the SmartPlanter application for current and future products.

### 8.3.2 SOURCE

Student pitched CSE Senior Design project specifications by group member Samuel Ruiz

### 8.3.3 CONSTRAINTS

Software team will include at least one employee on call a week for emergency software related issues.

### 8.3.4 STANDARDS

### 8.3.5 PRIORITY

Future

### 9 OTHER REQUIREMENTS

Our mobile application will use Flutter SDK in order for our app to be compatible with all platforms like iOS, Android, Windows, and macOS to name a few. We will have to use Dart as our programming language for our application since that is the default for Flutter.

### 9.1 MUST USE FLUTTER

### 9.1.1 DESCRIPTION

Flutter will be used to develop the mobile application in order for it to compatible for all platforms.

### 9.1.2 SOURCE

Samuel Ruiz

### 9.1.3 CONSTRAINTS

### 9.1.4 STANDARDS

### 9.1.5 PRIORITY

Critical

### 9.2 MUST USE DART PROGRAMMING LANGUAGE

### 9.2.1 DESCRIPTION

We will use Dart as our programming language to use the Flutter SDK.

### 9.2.2 SOURCE

Samuel Ruiz

### 9.2.3 CONSTRAINTS

### 9.2.4 STANDARDS

### 9.2.5 PRIORITY

Critical

### 10 FUTURE ITEMS

### 10.1 SOLAR POWER

### 10.1.1 DESCRIPTION

The SmartPlanter will include a solar panel along with a battery to remove the need for wires.

### 10.1.2 SOURCE

Student pitched CSE Senior Design project specifications by group member Samuel Ruiz

### 10.1.3 CONSTRAINTS

Adding solar panels might be ideal for the smart planter but will result in constraints on the sustainability of the battery. Keeping the LCD screen on will drain deplete the battery faster and cause the device to shut down during the night.

### 10.1.4 STANDARDS

We will be using the NEC wire color coding standards.

### 10.1.5 PRIORITY

Future (not feasible in this version of the product, but should be considered for a future release)

### 10.2 HELP DESK

### 10.2.1 DESCRIPTION

The SmartPlanter will require a help desk team to continue to provide support for the product. The help desk will include a small team of IT experts who can assist the customer with any issues with the device, identify if the issue is hardware or software related, and issue refunds/returns/repairs.

### 10.2.2 SOURCE

Student pitched CSE Senior Design project specifications by group member Samuel Ruiz

### 10.2.3 CONSTRAINTS

Help desk employees must be compensated at a reasonable hourly pay.

### 10.2.4 STANDARDS

Texas Minimum Wage Act

### 10.2.5 PRIORITY

Future

### 10.3 HARDWARE TEAM

### 10.3.1 DESCRIPTION

SmartPlanter will also include a hardware team to handle device repairs and returns due to hardware failure. Hardware team will identify any possible hardware failure and find solutions.

### 10.3.2 SOURCE

Student pitched CSE Senior Design project specifications by group member Samuel Ruiz

### 10.3.3 CONSTRAINTS

If hardware failure is due to customer then no replacements or repairs will take place.

### 10.3.4 PRIORITY

Future

### 10.4 SOFTWARE TEAM

### 10.4.1 DESCRIPTION

SmartPlanter will include a software developer team to handle software related issues and updates. The software team will continue to support the SmartPlanter application for current and future products.

### 10.4.2 SOURCE

Student pitched CSE Senior Design project specifications by group member Samuel Ruiz

### 10.4.3 PRIORITY

Future

### 10.5 INSTRUCTION MANUAL

### 10.5.1 DESCRIPTION

The instruction manual will have a step by step process on how to interface with the pot via mobile application. It will also have a contact support number in case they have any trouble setting up. A video link will be provided as well in order to see how to set up the pot.

### 10.5.2 SOURCE

Samuel Ruiz

### 10.5.3 CONSTRAINTS

The customer will need WiFi in order to connect the pot to the network.

### 10.5.4 PRIORITY

Future

### 10.6 BOX PACKAGE

### 10.6.1 DESCRIPTION

The smart planter will be stored in a box with different color choices for customers and the logo of Plant Ways.

### 10.6.2 SOURCE

Samuel Ruiz

### 10.6.3 CONSTRAINTS

Smart Planter will only be limited to certain colors.

### 10.6.4 STANDARDS

ISO 55.020 Packaging and Distribution of goods in general

### 10.6.5 PRIORITY

Future

### 10.7 ENCRYPTION FOR DATABASE

### 10.7.1 DESCRIPTION

Database will be encrypted in order to protect users information being leaked.

### 10.7.2 SOURCE

Samuel Ruiz

### 10.7.3 CONSTRAINTS

The limits to the security of the cloud database we service.

### 10.7.4 STANDARDS

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

### 10.7.5 PRIORITY

Future

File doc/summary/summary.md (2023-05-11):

### [< Back](/README.md) to README File

# Code Organization and File Structure

Code is organized under the following major files and directories:

```text

├── docs: Documentation.
|     └──  design
|            ├── design.md: Locate the design.
|            └── 3D print: Versions of Print for Smart Planter STL Files
|    └── documents: documentation for us.
|           ├── overleaf.md: documentation for Overleaf
|           └── pdfs : Recent PDF format for all Overleaf.
|               ├── ADS.pdf: Architecture Design Specification documentation.
|               ├── PC.pdf: Project Charter documentation.
|               └── SRS.pdf: System Requirement Specification documentation.
|    └── summary: summary for application
|       └── summary.md: Understand the file structure.
|
├── src: Source Code goes here
|    ├── plantsways_iot: IoT Source Code.
|    └── plantsways_app: Flutter Application Source Code.
|
├── CITATION: Developer Site
|
├── CONTRIBUTION: Developer Guide
|
├── LICENSE: BSD 3-Clause License
|
├── README: Overview page for Smart Planter: PlantWays
|
└── ... developer files (vscode, git, idea, etc)
```

## Code Style

Code (mostly) adheres to [Flutter Guide](https://docs.flutter.dev/):

- camelCase is used for variable names and modularized css classes
- `const` instead of `var` or `let` is employed wherever possible
- jsdoc comments are / should be included for each function/class/etc.

While no hard formatting rules are enforced, eg, indentation level, tab vs. space, max length, etc., the code is formatted in a way that is easy to read and modify.

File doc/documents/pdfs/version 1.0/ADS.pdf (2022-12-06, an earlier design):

## DEPARTMENT OF COMPUTER SCIENCE & ENGINEERING

## THE UNIVERSITY OF TEXAS AT ARLINGTON

## ARCHITECTURAL DESIGN SPECIFICATION

# CSE 4316: SENIOR DESIGN I FALL 2022


## PLANT WAYS

## SMARTPLANTER

SAMUEL J RUIZ
KEVIN FLORES
LUIS GUILLERMO JAEN
DON BUI
SAMRAT BARAL
Plant Ways - Fall 2022 | page 1 of 20

REVISION HISTORY

Revision | Date | Author(s) | Description
0.1 | 10.28.2022 | KF,DB,SR,LJ,SB | document creation
1.0 | 11.07.2022 | KF,DB,SR,LJ,SB | complete draft

CONTENTS

1 Introduction | 5
2 System Overview | 6
3 Subsystem Definitions & Data Flow | 8
4 Smart Planter Subsystems | 9
5 User Interface Layer Subsystem | 13
6 Cloud Layer Subsystems | 19

LIST OF FIGURES

1 | SmartPlanter architectural layer diagram | | 6
2 | Sub-system overview | | 8
3 | Subsystem description diagram | | 9
4 | Setup subsystem description diagram | | 13
5 | Setup subsystem | | 14
6 | Account subsystem | | 16
7 | Network subsystem | | 17
8 | Cloud subsystem description diagram | | 19

LIST OF TABLES

2 | Water pump interfaces | | 10
3 | Sensors interfaces | | 10
4 | WiFi interfaces | | 11
5 | Bluetooth interfaces | | 11
6 | LCD Screen interfaces | | 12
7 | Setup Subsystem Interfaces | | 15
8 | Setup Subsystem Interfaces | | 16
9 | Setup Subsystem Interfaces | | 18
10 | Subsystem interfaces | | 19
11 | Subsystem interfaces | | 20

### 1 INTRODUCTION

The SmartPlanter is a product intended to ease plant maintenance by monitoring the plants environment and automating the watering process. The SmartPlanter will require a mobile application that allows users to pair their SmartPlanter device to the internet. Using the mobile application, the users can set the sensor calibration data for the specific plant they are planting. The SmartPlanter device will be able to monitor the plant’s environment using the sensors and the calibration data in order to automate the watering process when the soil is too dry.

### 2 SYSTEM OVERVIEW

The SmartPlanter has three layers which consist of the SmartPlanter Layer, the User Interface layer or Phone Application Layer, and the Cloud Layer. The SmartPlanter layer consist of the physical plant pot and includes the micro-controller, water tank, sensors and LCD screen. The SmartPlanter layer monitors the plant’s environment and provides automatic watering. This layer also provides data to the Cloud Layer for storage. The User interface layer consist of a mobile phone application where the settings for the pot can be selected. This settings can be applied directly to the SmartPlanter Layer by communicating by Bluetooth. The User Interface layer can also access the SmartPlanter through the cloud layer using WiFi.


Figure 1: SmartPlanter architectural layer diagram

### 2.1 SMARTPLANTER

The SmartPlanter will have a display on the pot, that will let the user change the name on display or switch the display to show the current time. The SmartPlanter pot will have WiFi and Bluetooth. The WiFi is used to connect to the database and to upload data collected from the sensors. The Bluetooth feature will be used for the initial setup to connect it to the WiFi. The SmartPlanter pot will have a water pump used to water the plant when the soil moisture is detected low. The SmartPlanter will also include a light detector, a humidity and temperature sensor to monitor the average environment the plant is currently in and will upload the average data to the database. A water level detector will also be used to monitor the water tank level and assure it does not run below the minimum threshold. An LCD screen will also be included in the front of the SmartPlanter pot that displays either the name of the plant or the current time.

### 2.2 USER INTERFACE

The User Interface layer consist of mobile phone application that interfaces with the SmartPlanter via Bluetooth and the cloud via WiFi . The main usage of Bluetooth consist of the initial device set up to connect the SmartPlanter to the home network. The application will consist of an account subsystem to allow the user to change settings. The phone application can also change the calibration data of the SmartPlanter by adding custom settings catered to the plant they are growing. This is performed by allowing the user to connect to the cloud layer and view a database of plants. When this information is selected, it will store those calibration settings in the database and into the local storage of the Smart-Planter. The application can also view the current environmental conditions of the plant by connecting to the cloud through the network and then accessing the SmartPlanter.

### 2.3 CLOUD

The Cloud Layer consist of a database used to store plant sensor data from the SmartPlanter and user account settings from the User Interface Layer. The database will also store hard-coded plant information that the user will be able to retrieve via the mobile phone application.

### 3 SUBSYSTEM DEFINITIONS & DATA FLOW

The user would be able to connect to the smart planter through Bluetooth whenever they press the new device button in their application once connected they can set up their planter with their home WiFi. Once their account and planter are set up both devices are connected to the network where they can send and receive data from the database.


Figure 2: Sub-system overview

### 4 SMART PLANTER SUBSYSTEMS

In this section, the layer is described in some detail in terms of its specific subsystems. Describe each of the layers and its subsystems in a separate chapter/major subsection of this document. The content of each subsystem description should be similar. Include in this section any special considerations and/or trade-offs considered for the approach you have chosen.
The Smart Planter layer is made up of 5 different subsystems which gather information, communicate with other important functions like watering and online data, and display information to the user. The subsystems are the following: auto water pump system, sensor system, Bluetooth, WiFi, and the LCD screen.


Figure 3: Subsystem description diagram

### 4.1 AUTO WATER PUMP

The auto water pump subsystem is in charge of watering the plant and keeping the plant at a sufficient level of moisture. It communicates with the sensors in the planter, receiving the instruction to pump water.

### 4.1.1 ASSUMPTIONS

We assume the water pump successfully receives the signal to water the planter from the moisture sensor.

### 4.1.2 RESPONSIBILITIES

This water pump subsystem is responsible for keeping the plant at a sufficient level of moisture. When the soil runs too dry, the water pump will receive a signal from the moisture sensor, which will initiate the process of pumping the water into the soil.

### 4.1.3 WATER PUMP INTERFACES

Table 2: Water pump interfaces

ID | Description | Inputs | Outputs
#01 | Moisture Sensor | moisture level | water instruction

### 4.2 SENSORS

The sensors in our smart planter collect external and internal data which is used to monitor the current status of the plant. The sensors include: light, humidity, temperature, and soil moisture. The soil moisture sensor communicates with the water pump, telling it when to pump water, and the other 3 sensors send their data through WiFi to our cloud.

### 4.2.1 ASSUMPTIONS

We assume all of the sensors operate accurately, and correctly record data on the external and internal environments.

### 4.2.2 RESPONSIBILITIES

The light sensors are responsible for gathering data from the smart planter’s light environment, recording the light exposure on the plant. The humidity and temperature sensors are responsible for recording the humidity and temperature of the environment. The soil moisture sensor is in charge of keeping track of the moisture levels of the soil, notifying the water pump to water when the soil is too dry. All of these sensors communicate with our cloud database through WiFi.

### 4.2.3 SENSORS INTERFACES

Table 3: Sensors interfaces

ID | Description | Inputs | Outputs
#01 | Water Pump | power on for pump | water the planter

#01 | WiFi | Humidity, Temper-ature, Light Expo-sure Data | send data to cloud

### 4.3 WIFI

The WiFi component of our smart planter deals with receiving all of the data from the external and internal sensors, and then sending that data off to the cloud database. The WiFi communicates with the sensor subsystem and the LCD screen.

### 4.3.1 ASSUMPTIONS

We assume the networks are up and fully operational, and that there are no obstructions to the transmission of data.

### 4.3.2 RESPONSIBILITIES

The WiFi system is responsible for receiving the light exposure, temperature, and humidity levels, and sending them over to the cloud database. It is also responsible for receiving the current time from the network and sending it over to the LCD screen.

### 4.3.3 WIFI INTERFACES

Table 4: WiFi interfaces

ID | Description | Inputs | Outputs
#01 | Light Sensor | exposed light | lumen value

#02 | Humidity Sensor | environment hu-midity | humidity percent-age

#03 | Temperature Sensor | environment tem-perature | degrees Fahren-heit

#04 | LCD Screen | current time or plant name | current time or plant name on the screen

### 4.4 BLUETOOTH

The Bluetooth system is there to establish a connection between the smart planter and the network, via your smart phone. The Bluetooth communicates with the WiFi subsystem.

### 4.4.1 ASSUMPTIONS

We assume the Bluetooth technology is properly establishing connections between the smart planter and network.

### 4.4.2 RESPONSIBILITIES

The Bluetooth is responsible for establishing the network connection between the smart planter and WiFi, by using your smart phone to input the required information.

### 4.4.3 BLUETOOTH INTERFACES

Table 5: Bluetooth interfaces

ID | Description | Inputs | Outputs
#01 | Smart Phone | Bluetooth creden-tials | WiFi credentials

### 4.5 LCD SCREEN

The LCD screen is used to display either the current time or the name of your plant. The LCD screen communicates with the WiFi subsystem, receiving necessary data.

### 4.5.1 ASSUMPTIONS

We assume the LCD screen is posting the accurate plant name choice from the user, or the current time.
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

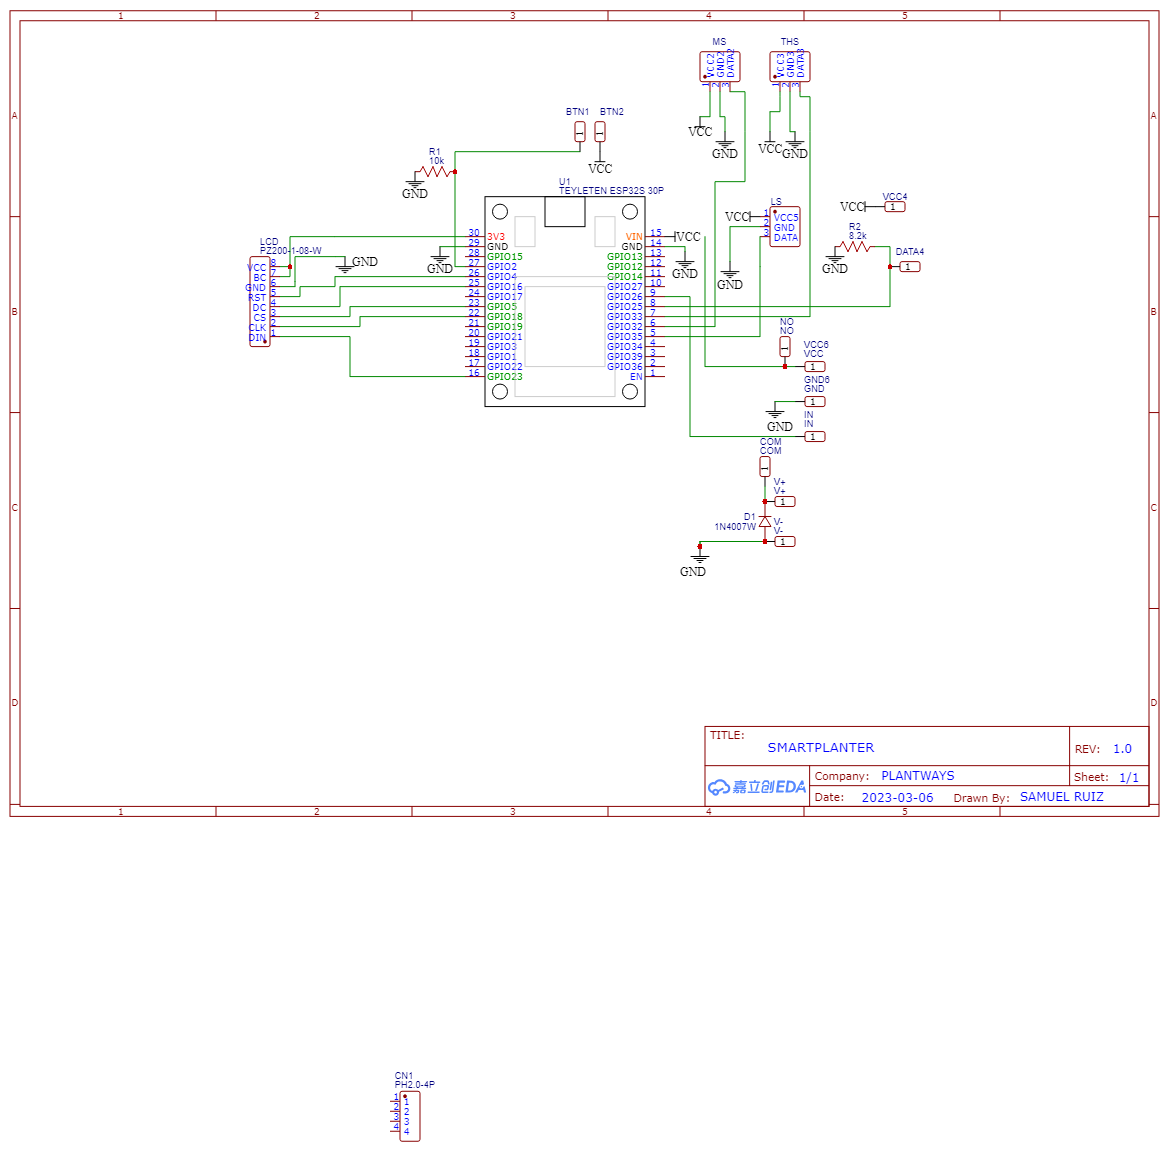
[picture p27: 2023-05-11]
src/plantsways_iot/PCB_Design/Schematic_SmartPlanter_2023-04-07.png

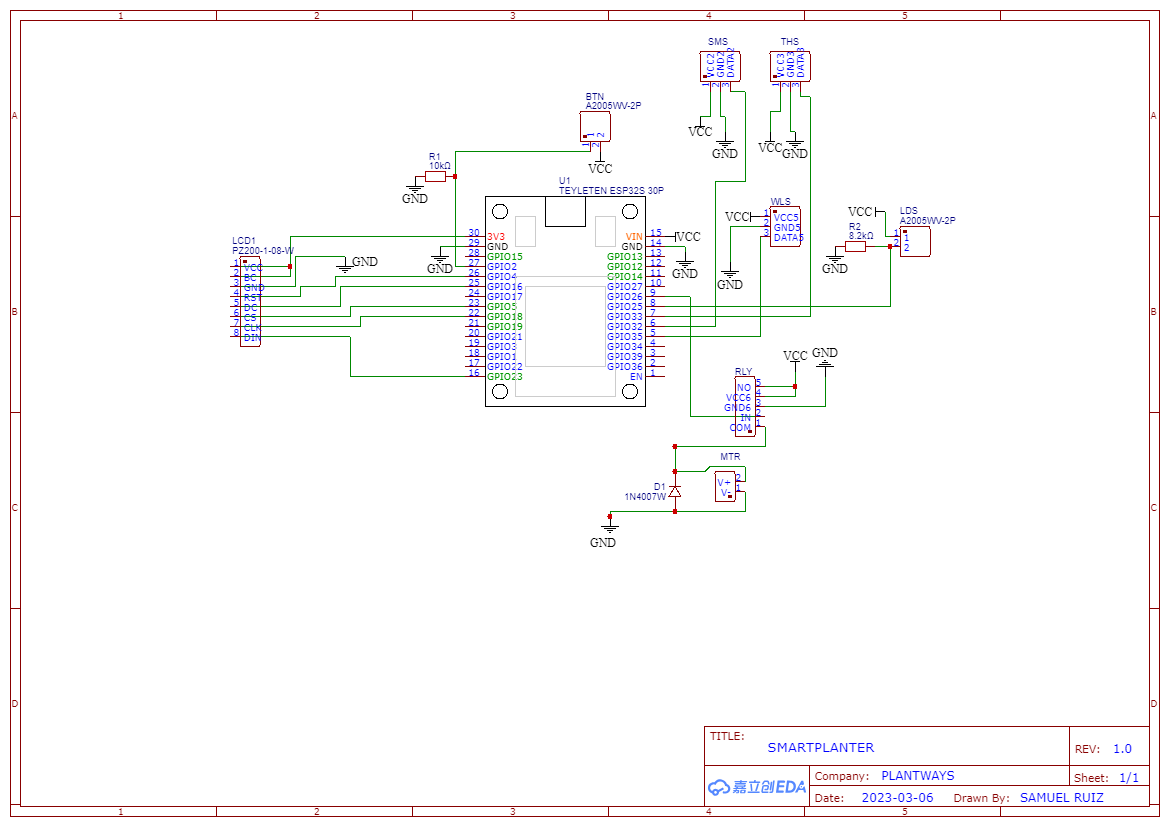
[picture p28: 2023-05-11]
src/plantsways_iot/PCB Final/Schematic_SmartPlanter2_2023-05-10.png

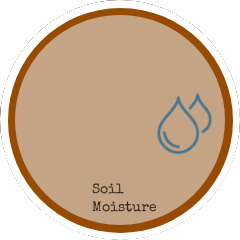
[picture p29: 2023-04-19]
src/plantways_app/Plantways-Application_client_20230317025249/assets/sensors/Sensor 2.png

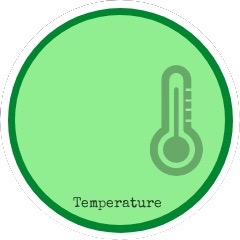
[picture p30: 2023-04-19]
src/plantways_app/Plantways-Application_client_20230317025249/assets/sensors/Sensor 3.jpeg

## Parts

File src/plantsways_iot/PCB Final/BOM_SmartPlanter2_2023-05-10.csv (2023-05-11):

ID | Name | Designator | Footprint | Quantity | Manufacturer Part | Manufacturer | Supplier | Supplier Part | Price
1 | A2005WV-2P | BTN,LDS | HDR-TH_2P-P2.00-V-M | 2 | A2005WV-2P | CJT(长江连接器) | LCSC | C225254 | 0.034
2 | 1N4007W | D1 | SOD-123_L2.8-W1.8-LS3.7-RD | 1 | 1N4007W | BLUE ROCKET | LCSC | C328592 | 0.006
3 | PZ200-1-08-W | LCD1 | HDR-TH_8P-P2.00-H-M-W7.2-N | 1 | PZ200-1-08-W | HCTL(华灿天禄) | LCSC | C2905974 | 0.055
4 | DB125-3.81-2P-BK-S | MTR | CONN-TH_2P-P3.81_DB125-3.81-2P-BK-S | 1 | DB125-3.81-2P-BK-S | DIBO(地博电气) | LCSC | C430618 | 0.175
5 | 10kΩ | R1 | RES-TH_BD4.5-L11.5-P15.50-D0.7 | 1 | MF2WS-10KΩ±1%T | 华星机电 | LCSC | C714145 | 0.028
6 | 8.2kΩ | R2 | RES-TH_BD5.0-L15.5-P19.50-D0.8 | 1 | MF2WS-8.2KΩ±1%T | 华星机电 | LCSC | C714144 | 0.029
7 | DB126V-5.0-5P-GN | RLY | CONN-TH_5P-P5.00-L8.0-W25.0 | 1 | DB126V-5.0-5P-GN-P | DIBO(地博电气) | LCSC | C2835160 | 0.223
8 | A2005WV-3P | SMS,THS,WLS | HDR-TH_3P-P2.00-V-M | 3 | A2005WV-3P | CJT(长江连接器) | LCSC | C225255 | 0.047
9 | TEYLETEN ESP32S 30P | U1 | ESP32S 30PIN DEVBOARD | 1 | ESP32 Development Board

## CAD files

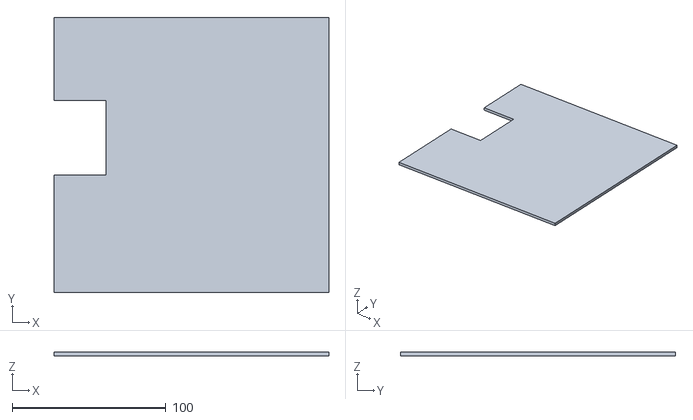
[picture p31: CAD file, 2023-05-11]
doc/designs/3D print/Version 4/water tank cover.stl
179.1 x 179.1 x 2.54

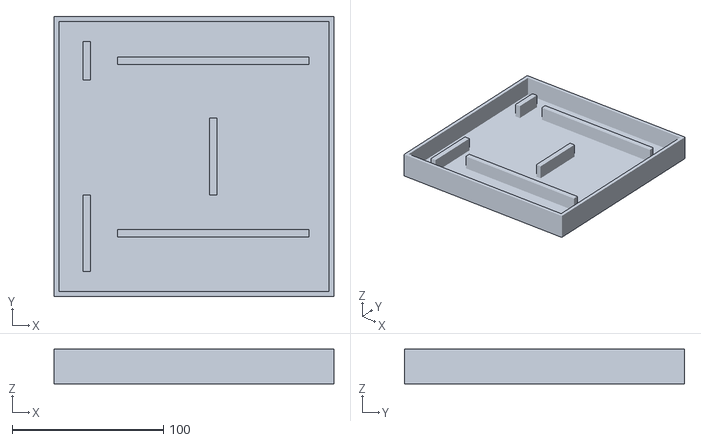
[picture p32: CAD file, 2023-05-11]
doc/designs/3D print/Version 4/water tank.stl
185.4 x 185.4 x 22.9

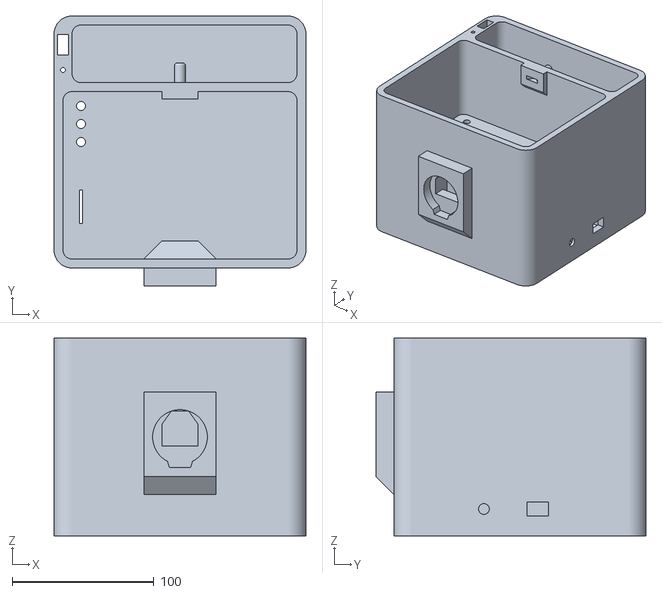
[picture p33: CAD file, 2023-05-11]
doc/designs/3D print/Version 4/pot v2.stl
177.8 x 190.5 x 139.7

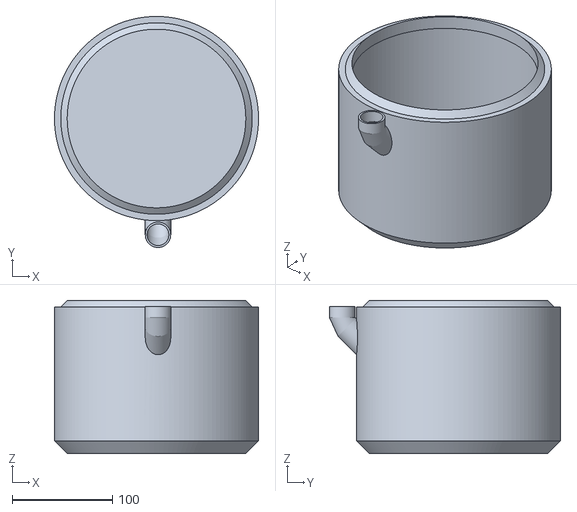
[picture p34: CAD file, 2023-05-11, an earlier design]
doc/designs/3D print/Version 1/pot v1 part 1.stl
203.2 x 230.0 x 152.4

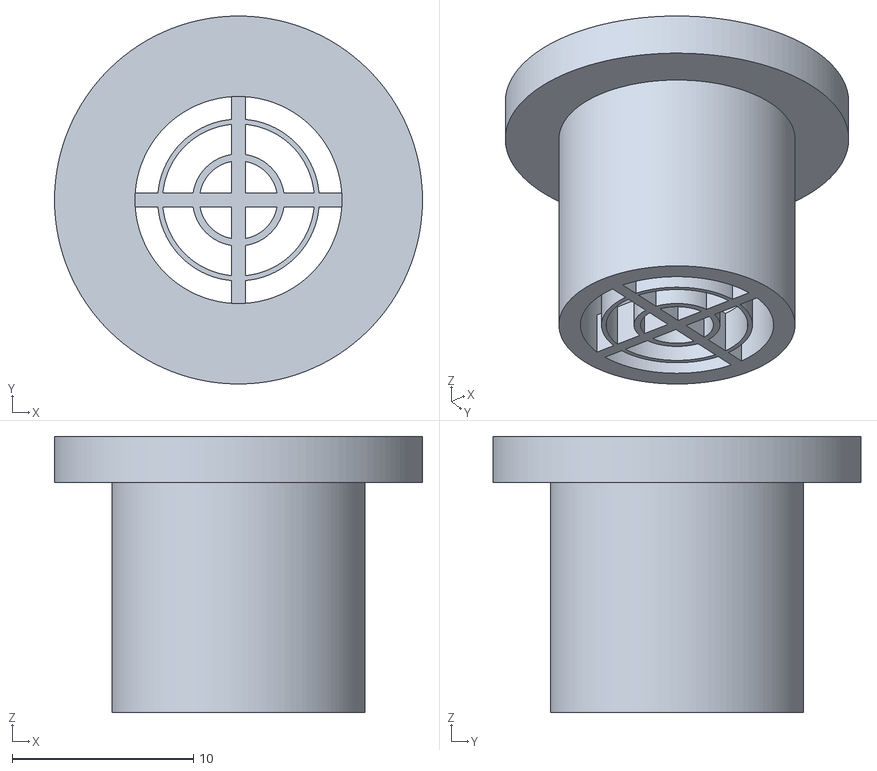
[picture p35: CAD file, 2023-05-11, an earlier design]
doc/designs/3D print/Version 3/water filter cover.stl
20.3 x 20.3 x 15.2

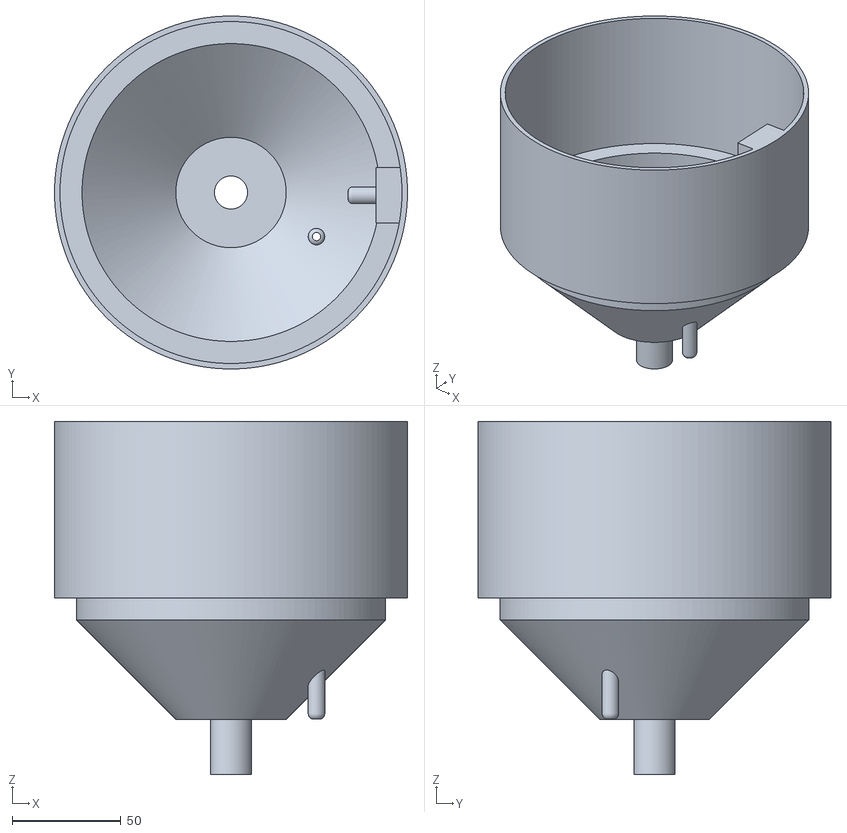
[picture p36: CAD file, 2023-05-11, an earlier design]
doc/designs/3D print/Version 1/pot v1 part 3.stl
162.6 x 162.5 x 162.6

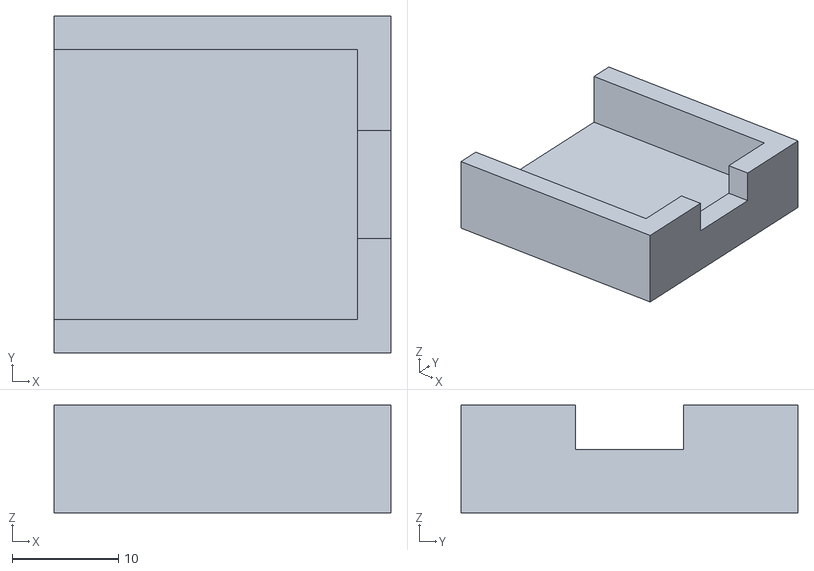
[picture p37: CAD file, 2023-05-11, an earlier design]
doc/designs/3D print/Version 3/sensor cover.stl
31.8 x 31.8 x 10.2

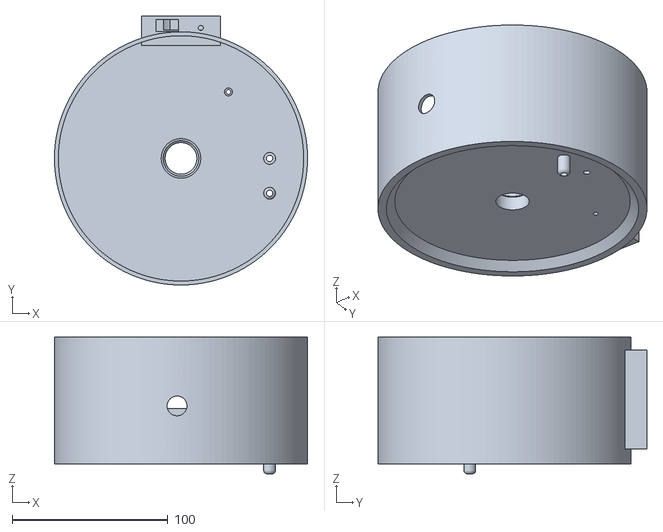
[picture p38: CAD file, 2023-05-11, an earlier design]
doc/designs/3D print/Version 1/pot v1 part 2.stl
162.6 x 172.7 x 87.7

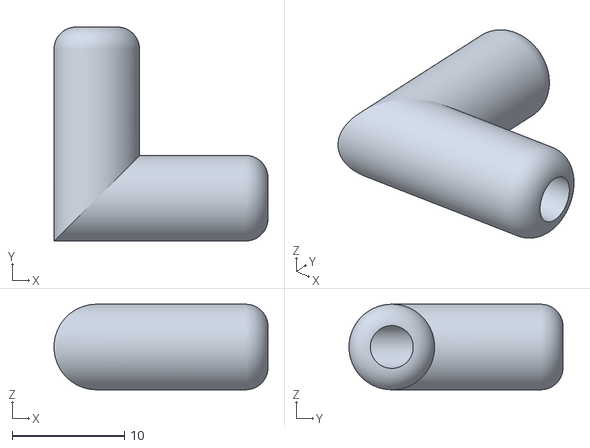
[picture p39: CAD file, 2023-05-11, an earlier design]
doc/designs/3D print/Version 3/pipe.stl
19.1 x 19.1 x 7.62

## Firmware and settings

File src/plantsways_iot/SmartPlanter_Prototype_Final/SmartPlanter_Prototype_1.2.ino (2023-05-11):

  
//====================================================================================
//                                    SmartPlanter
//====================================================================================
//SmartPlanter Project for UTA CSE 4317
//SmartPlanter was created by team PlantWays as a smart solution to taking care of 
//house plants. The SmartPlanter is able to automatically water the plant as well as
//monitor it's environment. The SmartPlanter is also an IoT device that allows for users
//to set up the calibration settings through a smartphone. From the application, users can
//select plants from the database to customize the amount of water the plant receives. 
//====================================================================================
//                                    Equipment
//====================================================================================
//Low Voltage Water Pump
//Capactive Soil Moisture Sensor
//5v Relay
//1N4007 Diode
//DHT11 Temperature and Moisture Sensor
//Photoresistor GL5516 LDR
//5k Ohm Resistor
//ESP32-Wroom-32
//Optical infrared Water Liquid Sensor
//1.28inch Round LCD IPS Module
//====================================================================================
//                           Libraries
//====================================================================================
#include <BLEDevice.h>
#include <BLEUtils.h>
#include <BLEServer.h>
#include <BLE2902.h>
#include <WiFi.h>
#include <HTTPClient.h>
#include <ArduinoJson.h>
#include <EEPROM.h>
#include "DHT.h" //DHT Library
#include <PNGdec.h> //PND Decoder
#include "gort.h" // Image is stored here in an 8 bit array
#include "logo.h"
#include "home.h"
#include "devscreen.h"
#include "temperature.h"
#include "humidity.h"
#include "light_exposure.h"
#include "soil_moisture.h"
#include "device_setup.h"
#include "SPI.h" // SPI Library for LCD
#include <TFT_eSPI.h>              // Hardware-specific library
#include "NotoSansBold36.h"  //Text Style for LCD Screen
#include <Preferences.h>
//====================================================================================
//                           ESP32 Pins
//====================================================================================
const int waterPumpPin = 26;
const int waterLevelPin = 35;
const int sunlightPin = 25;
const int soilMoisturePin = 32;
const int tempHumidityPin = 33;
const int bluetoothButtonPin = 13;
//ESP32 Pins enabled in User_Setup.h of the TFT Library
//#define TFT_MOSI 23 // In some display driver board, it might be written as "SDA" and so on.
//#define TFT_SCLK 18
//#define TFT_CS   5  // Chip select control pin
//#define TFT_DC   16  // Data Command control pin
//#define TFT_RST  4  // Reset pin (could connect to Arduino RESET pin)
//====================================================================================
//                           Sensor Globals
//====================================================================================
#define Type DHT11
DHT HT(tempHumidityPin,Type);
int setTime=500;
int dt=2000;

int waterLevel;
int lightLevel;
int moistureLevel;
float humidityLevel;
float temperatureLevel;

uint16_t  spr_width = 0;
uint16_t  bg_color =0;
//====================================================================================
//                           Bluetooth Globals
//====================================================================================
int bluetoothPairing;
#define SERVICE_UUID        "4fafc201-1fb5-459e-8fcc-c5c9c331914b"
#define CHARACTERISTIC_UUID "beb5483e-36e1-4688-b7f5-ea07361b26a8"

bool bleConnected = false;
bool wifiConnected = false;
bool deviceReady = false;
String nodata = "No data received";
BLECharacteristic *writeCharacteristic;
char* ssid; 
const char* password;
char* receivedData;
BLEServer *pServer;
BLEService *pService;
String mac_address;
String ssid_string;
String password_string;
//====================================================================================
//                           LCD Screen Globals
//====================================================================================
//#define GC9A01_DRIVER enabled in User_Setup.h of the TFT Library
PNG png; // PNG decoder inatance
#define MAX_IMAGE_WDITH 240 // Adjust for your images
int16_t xpos = 0;
int16_t ypos = 0;
// Include the TFT library https://github.com/Bodmer/TFT_eSPI
TFT_eSPI tft = TFT_eSPI();         // Invoke custom library
TFT_eSprite spr    = TFT_eSprite(&tft); // Sprite for meter reading
// Font attached to this sketch
#define AA_FONT_LARGE NotoSansBold36
//====================================================================================
//                           PREFERENCES
//====================================================================================
Preferences preferences;
//====================================================================================
//                          PNG Draw
//====================================================================================
// This next function will be called during decoding of the png file to
// render each image line to the TFT.  If you use a different TFT library
// you will need to adapt this function to suit.
// Callback function to draw pixels to the display
//====================================================================================
void pngDraw(PNGDRAW *pDraw) {
  uint16_t lineBuffer[MAX_IMAGE_WDITH];
  png.getLineAsRGB565(pDraw, lineBuffer, PNG_RGB565_BIG_ENDIAN, 0xffffffff);
  tft.pushImage(xpos, ypos + pDraw->y, pDraw->iWidth, 1, lineBuffer);
}
//====================================================================================
//                           Automatic Water Pump Function
//====================================================================================
//Waters the planter when soil moisture is low
//Shuts off water pump if water level is too low to avoid damage to the motor
//Moisture values will need to be extracted from database for indivudual plants
//====================================================================================
void runWaterPump()
{
  moistureLevel = analogRead(soilMoisturePin);
  Serial.print("Moisture Level: ");
  Serial.print(moistureLevel);
  Serial.print('\n'); 
  delay(1000);
  waterLevel = analogRead(waterLevelPin);
  Serial.print("Water Level: ");
  Serial.print(waterLevel);
  Serial.print("\n");
  delay(2000);
 if(moistureLevel >= 3000){
  
   if(waterLevel <= 1000){
     digitalWrite(waterPumpPin, HIGH);
     Serial.print("Motor ON\n ");
     tft.fillScreen(TFT_RED);
     tft.setTextColor(TFT_WHITE, 0);
     tft.setTextDatum(MC_DATUM);
     tft.drawString("(Watering)", 120, 120 + 48, 2);
     delay(1500);
     digitalWrite(waterPumpPin, LOW);
     Serial.print("Motor OFF\n ");

   }
   else{
     Serial.print("LOW WATER");
     tft.fillScreen(TFT_RED);
     tft.setTextColor(TFT_WHITE, 0);
     tft.setTextDatum(MC_DATUM);
     tft.drawString("(LOW WATER)", 120, 120 + 48, 2);
   }
   moistureLevel = analogRead(soilMoisturePin);
   delay(1000);
   waterLevel = analogRead(waterLevelPin);
   delay(1000);
   
 }
}
//====================================================================================
//                           Temperature Function
//====================================================================================
//Measures the temperature reading from the DHT11 Sensor
//====================================================================================
void getTemperature(){

  temperatureLevel = (HT.readTemperature(true));
  Serial.print("Temperature ");
  Serial.print(temperatureLevel);
  Serial.println(" F ");
  
  delay(1000);

}
//====================================================================================
//                          Humidity Function
//====================================================================================
//Measures the temperature reading from the DHT11 Sensor
//====================================================================================
void getHumidity(){
  humidityLevel = HT.readHumidity();
  Serial.print("Humidity: ");
  Serial.print(humidityLevel);
  Serial.print('\n'); 
  delay(dt);
  delay(1000);
}
//====================================================================================
//                          Sunlight Function
//====================================================================================
//Measures the light level from the photoresistor
//====================================================================================
void getLightLevel()
{
  //This code checks the light sensor value and prints out the amount of sunlight
  //Hardcoded values were recorded by measuring the analog read at different lighting
  
  //Needs more obtimization since esp32 reads in different values than the arduino
  int light = analogRead(25);
  Serial.println(light);
  delay(100);
}
//====================================================================================
//                          LCD DevScreen
//====================================================================================
//Dev screen is used to get an LCD screen of all the raw measurement data
//This will be used to easily calibrate the prototype with real soil and sunlight
//====================================================================================
void devScreen(){
  int16_t rc = png.openFLASH((uint8_t *)devscreen, sizeof(devscreen), pngDraw);
  if (rc == PNG_SUCCESS) {
    tft.startWrite();
    uint32_t dt = millis();
    rc = png.decode(NULL, 0);
    tft.endWrite();  
    // png.close(); // not needed for memory->memory decode
     // Plot the label text
    tft.setTextColor(TFT_WHITE);
    tft.setTextDatum(MC_DATUM);
    tft.drawString(String(temperatureLevel), 170, 76, 4);
    tft.drawString(String(humidityLevel), 170, 98, 4);
    tft.drawString(String(lightLevel), 170, 122, 4);
    tft.drawString(String(waterLevel), 170, 146, 4);
    tft.drawString(String(moistureLevel), 170, 170, 4);
    }

    delay(1000);
}
//====================================================================================
//                          LCD Home 
//====================================================================================
//Function is used to display homescreen for the LCD Display
//====================================================================================
void displayHomePage() {
  //Get time
  struct tm timeinfo;
  char time_buf[64];
  char date_buf[64];
  getLocalTime(&timeinfo);
  strftime(time_buf, sizeof(time_buf), "%I:%M%p", &timeinfo);
  strftime(date_buf, sizeof(date_buf), "%B %d, %Y", &timeinfo);

  int16_t rc = png.openFLASH((uint8_t *)home, sizeof(home), pngDraw);
  if (rc == PNG_SUCCESS) {
    tft.startWrite();
    uint32_t dt = millis();
    rc = png.decode(NULL, 0);
    tft.endWrite();

    //Time Sprite
    TFT_eSprite timeSpr = TFT_eSprite(&tft);  // Sprite for meter reading
    timeSpr.setColorDepth(8);
    timeSpr.loadFont(AA_FONT_LARGE);
    spr_width = timeSpr.textWidth("777");
    timeSpr.createSprite(spr_width * 8, timeSpr.fontHeight() * 8);
    timeSpr.fillSprite(TFT_BLACK);
    timeSpr.setTextDatum(MC_DATUM);
    timeSpr.setTextColor(TFT_WHITE, TFT_BLACK);
    timeSpr.setCursor(0, 0);
    timeSpr.setTextPadding(spr_width);
    timeSpr.setTextSize(4);
    //Date sprite
    TFT_eSprite dateSpr = TFT_eSprite(&tft);  // Sprite for meter reading
    dateSpr.setColorDepth(8);
    dateSpr.loadFont(AA_FONT_LARGE);
    spr_width = dateSpr.textWidth("777");
    dateSpr.createSprite(spr_width * 2, dateSpr.fontHeight() * 2);
    dateSpr.fillSprite(TFT_BLACK);
    dateSpr.setTextDatum(MC_DATUM);
    dateSpr.setTextColor(TFT_WHITE, TFT_BLACK);
    dateSpr.setCursor(0, 0);
    dateSpr.setTextPadding(spr_width);
    dateSpr.setTextSize(2);


    tft.drawString(time_buf, 120, 100, 4);  //(string, x, y , ?)
    tft.drawString(date_buf, 120, 120 + 10, 4);
  }
  delay(5000);
}
//====================================================================================
//                          LCD Temperature
//====================================================================================
//Function is used to display temperature for the LCD Display
//====================================================================================
void displayTemperature(){
       // Plot the label text
    int16_t rc = png.openFLASH((uint8_t *)temperature, sizeof(temperature), pngDraw);
    if (rc == PNG_SUCCESS) {
    tft.startWrite();
    uint32_t dt = millis();
    rc = png.decode(NULL, 0);
    tft.endWrite();  
    }
    // Update the number at the centre of the dial
    tft.setTextColor(TFT_WHITE);
    tft.setTextDatum(MC_DATUM);
    tft.drawString(String((int)temperatureLevel), 100, 120, 8);
    delay(2000);
}
//====================================================================================
//                          LCD Humidity
//====================================================================================
//Function is used to display humidity for the LCD Display
//====================================================================================
void displayHumidity(){
       // Plot the label text
    int16_t rc = png.openFLASH((uint8_t *)humidity, sizeof(humidity), pngDraw);
  if (rc == PNG_SUCCESS) {
    tft.startWrite();
    uint32_t dt = millis();
    rc = png.decode(NULL, 0);
    tft.endWrite();  
  }
    // Update the number at the centre of the dial
    tft.setTextColor(TFT_WHITE);
    tft.setTextDatum(MC_DATUM);
    tft.drawString(String((int)humidityLevel), 100, 120, 8);
    delay(2000);
}
//====================================================================================
//                          LCD Sunlight
//====================================================================================
//Function is used to display Sunlight for the LCD Display
//====================================================================================
void displaySunlight(){
       // Plot the label text
    int16_t rc = png.openFLASH((uint8_t *)light_exposure, sizeof(light_exposure), pngDraw);
  if (rc == PNG_SUCCESS) {
    tft.startWrite();
    uint32_t dt = millis();
    rc = png.decode(NULL, 0);
    tft.endWrite();  
  }
    // Update the number at the centre of the dial
    tft.setTextColor(TFT_WHITE);
    tft.setTextDatum(MC_DATUM);
    tft.drawString("(OK)", 120, 120 + 48, 2);
    delay(2000);
}
//====================================================================================
//                          LCD Moisture
//====================================================================================
//Function is used to display Moisture for the LCD Display
//====================================================================================
void displayMoisture(){
       // Plot the label text
    int16_t rc = png.openFLASH((uint8_t *)soil_moisture, sizeof(soil_moisture), pngDraw);
  if (rc == PNG_SUCCESS) {
    tft.startWrite();
    uint32_t dt = millis();
    rc = png.decode(NULL, 0);
    tft.endWrite();  
  }
    // Update the number at the centre of the dial
    tft.setTextColor(TFT_WHITE);
    tft.setTextDatum(MC_DATUM);
    if(moistureLevel >= 2500){
      tft.drawString("(DRY)", 120, 120 + 48, 2);
    }
    else {
      tft.drawString("(OK)", 120, 120 + 48, 2);
    }
    delay(2000);
}
//====================================================================================
//                          Device Setup
//====================================================================================
//Function is used to display the device set up page
//====================================================================================
void displayDeviceSetup(){
    int16_t rc = png.openFLASH((uint8_t *)device_setup, sizeof(device_setup), pngDraw);
    if (rc == PNG_SUCCESS) {
    tft.startWrite();
    uint32_t dt = millis();
    rc = png.decode(NULL, 0);
    tft.endWrite();  
    }
}
void displayBlePairing(){
      tft.fillScreen(TFT_BLACK);
      tft.setTextColor(TFT_WHITE, 0);
      tft.setTextDatum(MC_DATUM);
      tft.drawString("(BLE PAIRING ON)", 120, 120 + 48, 2);
}
void displayWifiPairing(){
      tft.fillScreen(TFT_BLACK);
      tft.setTextColor(TFT_WHITE, 0);
      tft.setTextDatum(MC_DATUM);
      tft.drawString("(CONNECTING WIFI)", 120, 120 + 48, 2);
}
//====================================================================================
//                          MongoDB
//====================================================================================
//Function is used to post sensor data into database
//====================================================================================
void postData(){
  StaticJsonDocument<1024> docUpdate;
  docUpdate["dataSource"] = "PlantWays";
  docUpdate["database"] = "todo";
  docUpdate["collection"] = "PlantUserData";
  JsonObject filter = docUpdate.createNestedObject("filter");
  filter["potMac"] = mac_address;
  JsonObject updateInfo = docUpdate.createNestedObject("update");
  JsonObject setInfo = updateInfo.createNestedObject("$set");
  JsonArray potSensorData = setInfo.createNestedArray("potSensorData");
  potSensorData.add("High Humidity");
  potSensorData.add("High Light");
  potSensorData.add("Moist Soil");
  potSensorData.add("High Level");
  potSensorData.add("High Temperature");

  String json, jsonUpdate;
  serializeJson(docUpdate, jsonUpdate);

  if(WiFi.status() == WL_CONNECTED){

    HTTPClient http;
    int httpResponseCode;
    http.begin(" ");
    http.addHeader("Content-Type", "application/json");
    http.addHeader("apiKey", " ");
    httpResponseCode = http.POST(jsonUpdate);
    Serial.print("Updating document (status code): ");
    Serial.println(httpResponseCode);
    http.end();
  }
}
//====================================================================================
//                          WIFI
//====================================================================================
//Function is used to connect ESP32 to internet through wifi
//====================================================================================
void connectToWifi(){
 char ssid_char[32], password_char[32];
  
  strcpy(ssid_char, ssid);
  strcpy(password_char, password);
 WiFi.begin(ssid_char, password_char);
 uint8_t count = 0;
 while(WiFi.status() != WL_CONNECTED){
   delay(1000);
   //Serial.println("Connecting to WiFi...attempt: " + count);
   Serial.println("Connecting to WiFi...attempt: ");
   Serial.println(ssid_char);
   Serial.println(password_char);
  //  count++;
  //  if(count == 10){
  //    break;
  //  }
  }
  // if(WiFi.status() == WL_CONNECTED){
    Serial.println("Connected to WiFi");
    wifiConnected = true;
    ssid_string = String(ssid);
    password_string = String(password);
    preferences.putString("ssid",ssid_string);
    preferences.putString("password",password_string);
  // }
configTime(-21600, 3600, "pool.ntp.org");  //Central Timezone
}
//====================================================================================
//                          BLUETOOTH
//====================================================================================
//Functions are used to open bluetooth connection and wait until there is a call back
//====================================================================================
class MyServerCallbacks : public BLEServerCallbacks{
 void onConnect(BLEServer* pServer){
 };
};

class onWriteCallback : public BLECharacteristicCallbacks{
 void onWrite(BLECharacteristic *pCharacteristic){
   receivedData = const_cast<char*>(pCharacteristic -> getValue().c_str());
  //  char* ssidChar = strtok(receivedData, ",");
  //  const char* passwordChar = strtok(NULL, ",");
  //  ssid = ssidChar;
  //  password = passwordChar;
  ssid = strtok(receivedData, ",");
  password = strtok(NULL, ",");
   Serial.println(ssid);
   Serial.println(password);
   //if((ssidChar == NULL)||(passwordChar == NULL)){
    if((ssid == NULL)||(password == NULL)){
     Serial.println("Issues with wifi credentials passed from app");
   }
   else{
    bleConnected = true;
   connectToWifi();
   }
 }; 
};
void startBluetoothPairing(){
  displayBlePairing();
  BLEDevice::init("SmartPlanter");
  BLEAddress bleAddress = BLEDevice::getAddress();
  mac_address = String(bleAddress.toString().c_str());
  Serial.println(mac_address);
  pServer = BLEDevice::createServer();
  pServer -> setCallbacks(new MyServerCallbacks());
  pService = pServer->createService(SERVICE_UUID);
 writeCharacteristic = pService->createCharacteristic(
                                        CHARACTERISTIC_UUID,
                                        BLECharacteristic::PROPERTY_READ |
                                        BLECharacteristic::PROPERTY_WRITE
                                      );
 writeCharacteristic->setValue("WRITE_HERE");
 writeCharacteristic->setCallbacks(new onWriteCallback());
 pService->start();
 // BLEAdvertising *pAdvertising = pServer->getAdvertising();  // this still is working for backward compatibility
 BLEAdvertising *pAdvertising = BLEDevice::getAdvertising();
 pAdvertising->addServiceUUID(SERVICE_UUID);
 pAdvertising->setScanResponse(true);
 pAdvertising->setMinPreferred(0x06);  // functions that help with iPhone connections issue
 pAdvertising->setMinPreferred(0x12);
 BLEDevice::startAdvertising();
}
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
void loop() {


  
  getTemperature();
  displayTemperature();
 
  getHumidity();
  displayHumidity();
  
  getLightLevel();
  displaySunlight();
  
  runWaterPump();
  displayMoisture();
  
  //devScreen();
  displayHomePage();
  delay(10000);
  postData();


}

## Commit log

2023-04-24 Major Update on UI. Scan Button Added on Add Planter Form
2023-05-11 Added 3d design
    [pipe.stl, pot v1 part 1.stl, pot v1 part 2.stl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]
2023-05-11 Added Documentation, Readme Change
    [pipe.stl, pot v1 part 1.stl, pot v1 part 2.stl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]
2023-05-11 Add files via upload
    Final 3D Design
    [pot v2.stl, water tank cover.stl, water tank.stl]
2023-05-11 Added Missing Docs and Code
    [BOM_SmartPlanter2_2023-05-10.csv, PickAndPlace_PCB_SmartPlanter2_2023-05-10.csv, pipe.stl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]
2023-05-11 Clean Up
    [pot v2.stl, water tank cover.stl, water tank.stl]
